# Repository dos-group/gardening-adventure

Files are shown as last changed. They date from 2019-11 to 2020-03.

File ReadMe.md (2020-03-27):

Documentation for Urban Gardening

# Table of Contents

- [Table of Contents](#table-of-contents)
- [Introduction](#introduction)
- [Prerequisites & Components](#prerequisites--components)
  - [Components listed per greenhouse](#components-listed-per-greenhouse)
- [Initial Setup](#initial-setup)
- [Installation & Setup](#installation--setup)
  - [Mesh Gateway Setup](#mesh-gateway-setup)
  - [Mesh Node Setup](#mesh-node-setup)
  - [Setting up the Cloud Environment](#setting-up-the-cloud-environment)
    - [Helm Deployment](#helm-deployment)
    - [Post Deployment Steps](#post-deployment-steps)
      - [Connecting Grafana with Influxdb](#connecting-grafana-with-influxdb)
      - [Grafana Charts](#grafana-charts)
      - [Grafana Alerts](#grafana-alerts)
        - [Create a Telegram Altert](#create-a-telegram-altert)
  - [Setting up the Greenhouse Environment](#setting-up-the-greenhouse-environment)
    - [Connecting Sensors](#connecting-sensors)
  - [Docker Sensor Images](#docker-sensor-images)
    - [Camera Configuration Options](#camera-configuration-options)
    - [Start Sensor and Actuators](#start-sensor-and-actuators)
- [Reference](#reference)

# Introduction

This project provides an infrastructure to implement a self sustaining smart garden. It uses state-of-the-art technologies to implement a variety of useful tools to monitor, alert and explore on the basis of the data.
The core of our work is the implementation of a greenhouse which provides sensors and actuators controlled via cloud systems to provide an optimal environment for plants.

In figure 1 we can see in the general overview the idea to connect multiple greenhouses via a wifi network mesh to a Cloud service. Whereby particular greenhouses can serves as a gateway and are directly connected to the cloud.
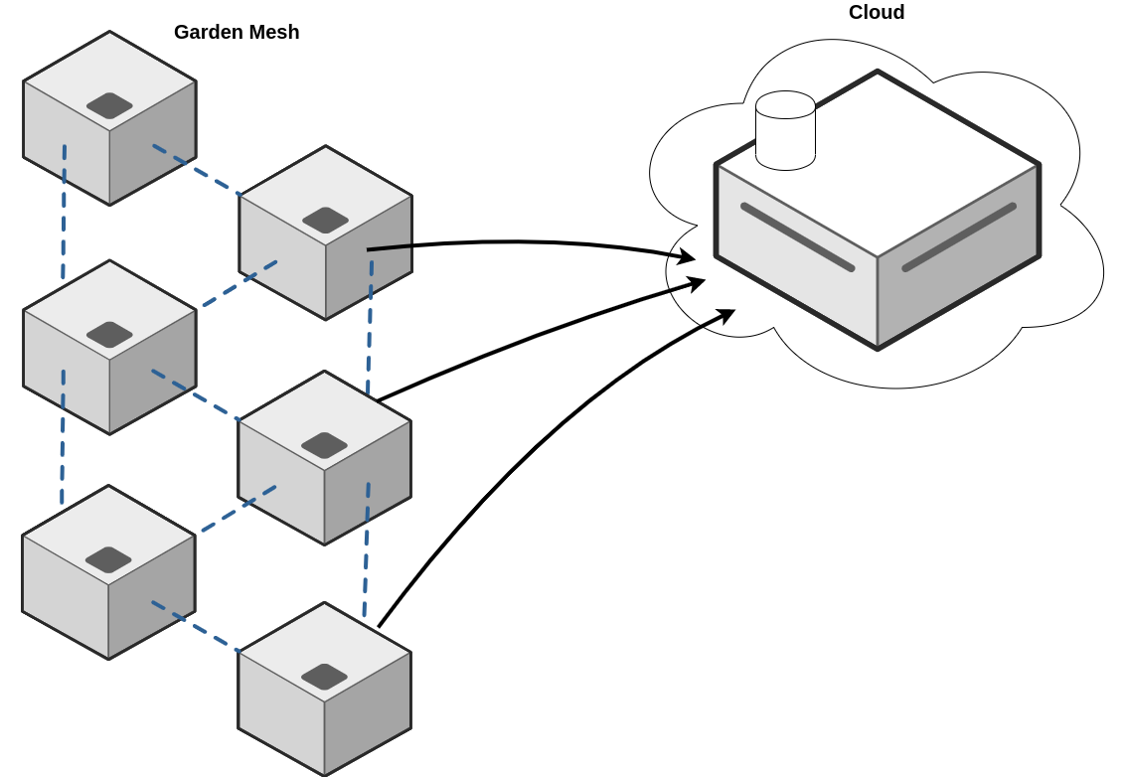
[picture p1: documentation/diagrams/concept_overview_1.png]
Overview


The greenhouses themselves contain a variety of sensors and actuators, as shown in figure 2. These sensors and actuators are connected via the GPIO connectors to an Raspberry pi.  The Raspberry pi gathers the sensor data and distributes this data via the above mentioned mesh network. The Pi also receives instructions for the connected actuators and executes them.
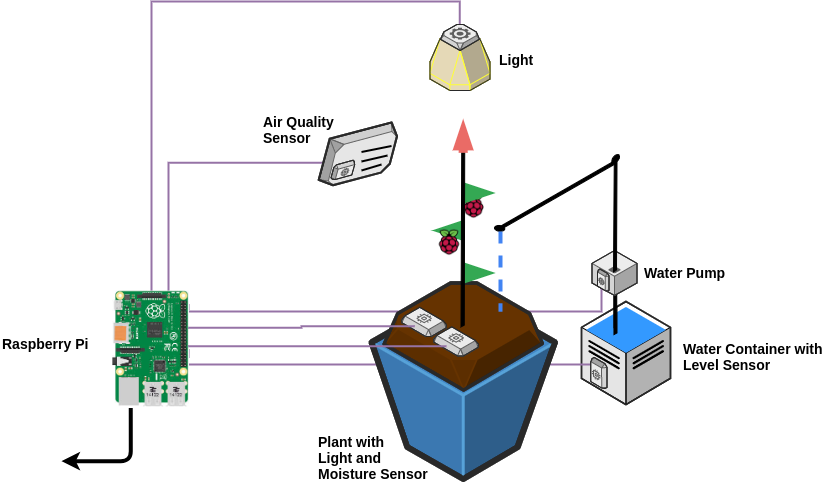
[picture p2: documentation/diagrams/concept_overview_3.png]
Overview


Figure 3 gives an overview about the Software implementation. In the lower part we see Multiple Pi's which implement the mesh network via [B.A.T.M.A.N](https://www.open-mesh.org/projects/open-mesh/wiki) (better approach to mobile ad-hoc networking) is a routing protocol for multi-hop ad-hoc mesh networks. The sensor & actuator logic is implemented via Python and containerized in [Docker](https://www.docker.com/). Each Raspberry is a Worker Node in a [K3s](https://k3s.io/) cluster.  K3s is a lightweight Kubernetes built for IoT & Edge computing. It perfect to for running on something as small as a Raspberry Pi.  
The sensor communication is realized via [MQTT](http://mqtt.org/). In particular we use [Paho mqtt](https://www.eclipse.org/paho/) for pyhton on the Pi side and a Mosquitto MQTT Broker on the cloud side. 
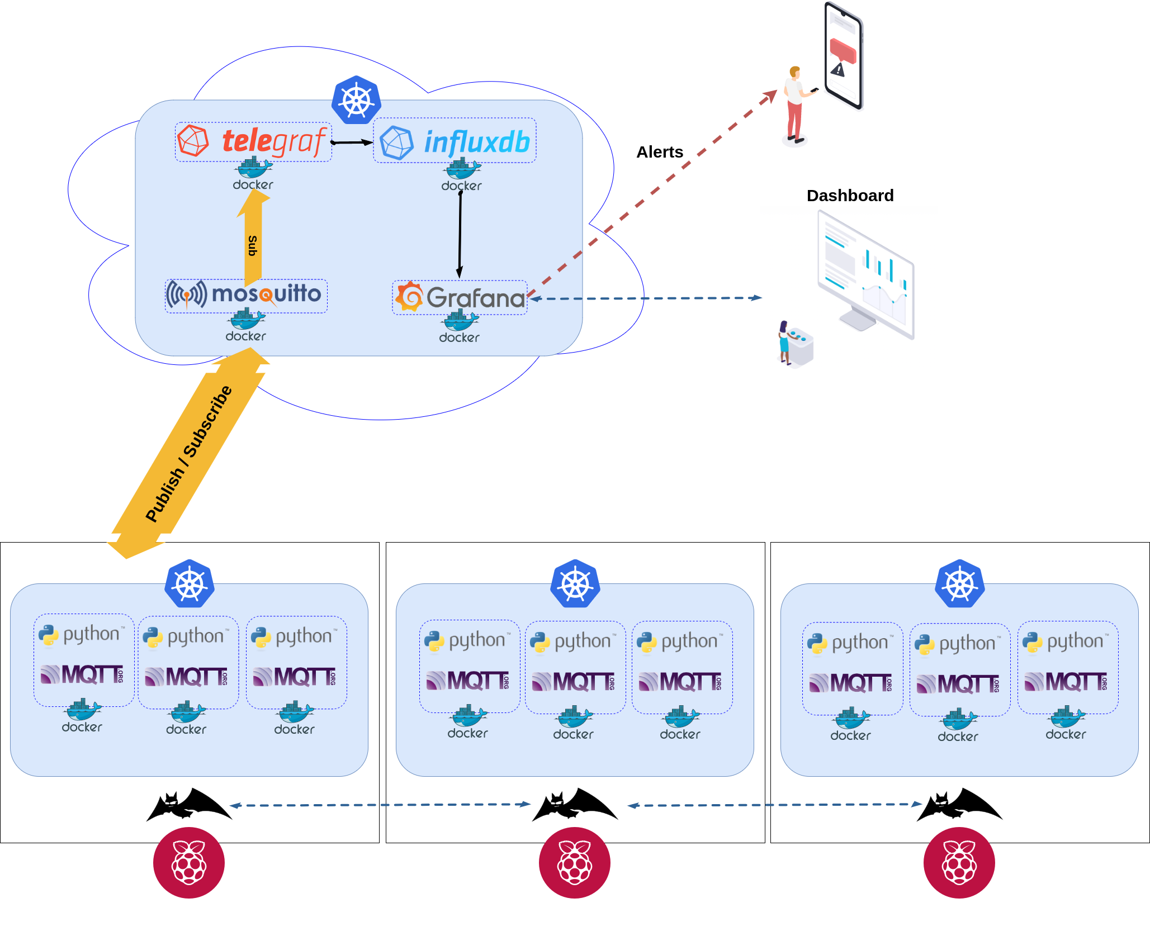
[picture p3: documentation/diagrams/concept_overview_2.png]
Overview

The cloud environment  consists of four services. A [Mosquitto](https://mosquitto.org/man/mqtt-7.html) MQTT broker for the communication with the greenhouse instances. [Telegraf](https://www.influxdata.com/time-series-platform/telegraf/) which subscribes to the published topics by the greenhouse sensors and  saves the data in an [influxdb](https://www.influxdata.com/) database. And lastly [Grafana](https://grafana.com/) which is used for data visualization and alerting.

# Prerequisites & Components

For the creation of the project we used a desktop computer as cloud environment(Master node) and raspberry pi's as worker nodes

## Components listed per greenhouse

| Component | Description |
| --- | --- |
| Raspberry Pi 3B / 4 | - |
| MicroSD Card 32GB | - |
| DHT22 Sensor | Temperature & Humidity Sensor |
| Water Level Sensor | Analog Water Level Sensor |
| Soil Moisture Sensor | Analog Soil Moisture Sensor |
| LDR | Light Dependent Resistor |
| MCP3008 | 8 Channel 10-bit ADC |
| Breadboard | 1 Piece |
| Male to Male Connectors | 100 Pieces |
| Male to Female Connectors | 100 Pieces |
| 5v Power Supply | Power supply for Raspberry Pi. 2.5A Power Supply recommended |
| 5v Waterpump | Water pump (Not implemented) |
| RGB LED | NeoPixel Ring - 12 x RGB LED |
| Jumper-Cabel | 5v power supply for LED |

# Initial Setup

Custom raspbian OS creation is part of this repository which installs necessary packages and configurations for setting up `gateway` and `node` Pis respectively. The configuration files are listed under the folder `batman`. These files could further be modified according to the needs of the project. Also the image creation, requires Ubuntu/Debian OS.

To create an image:

1. Clone this git repository

2. Run the script build-batman-node.sh in the folder `garden-adventure`

  ```bash
        ./build-batman-node.sh -t [gateway|node] -n [hostname] -u [k3s_url] -k [k3s_token] -d [dns_ip]
  ```

Specify the required options for the above command(type, hostname, k3s url, k3s token). Mention your dns_ip when creating an image for `node`(eg: 8.8.8.8).

* The above command downloads the base image of raspbian STRETCH. This base image can be modified as per the needs by changing the base image url in the file `build-raspbian`.
* Further, the command creates two installation scripts under the root user as part of each image(gateway/node).
* Root user is created with the password `raspberry`. This can also be modified in the file `build-batman-node.sh`
* The image created, has only limited firmwares installed that are necessary for the project(`brcm` for wlan interface). Other firmwares could be installed from [here](https://github.com/RPi-Distro/firmware-nonfree). They should be copied at the time of image creation. Refer the script `build-batman-node.sh`.

# Installation & Setup

Using Raspberry Pi Imager, burn the created image onto a SD card. The created image could be found under the folder `images` after running above script.

- Writing the Raspbian Image to the SD Card
  - [Windows](https://www.raspberrypi.org/documentation/installation/installing-images/windows.md)
  - [Linux](https://www.raspberrypi.org/documentation/installation/installing-images/linux.md)
  - [MacOS](https://www.raspberrypi.org/documentation/installation/installing-images/mac.md)
  - [ChromeOS](https://www.raspberrypi.org/documentation/installation/installing-images/chromeos.md)

## Mesh Gateway Setup

First setup the gateway Pi by connecting it to ethernet and inserting the SD card that contains the raspbian OS for gateway and powering it on. The first boot steps will be performed and you can login with the details provided above. Under the root user following scripts can be found:

1. smart-garden-mesh.sh

2. k3s_installation.sh

Running the first script, brings up the B.A.T.M.A.N inteface for mesh network along with the Pi configured as a gateway. It starts a dhcp server for the inteface `bat0` and enables a custom service called `port-forwarding.service` that forwards packets across batman and ethernet interface.

Running the second script, installs K3s and adds the Pi as a worker to a K3s cluster. If the k3s master is not part of the same network as gateway and belongs to the public network, then k3s installation should be done via VPN. This is currently out of the scope of this repository. Refer [OpenVPN](https://openvpn.net/) or [Wiregaurd](https://www.wireguard.com/) for more information about setting up VPN.

## Mesh Node Setup

Setup the node by inserting the SD card that contains the raspbian OS for the node. The ethernet connection is not needed for the node setup. Also under the root user, the above mentioned scripts could be found.

1. First run smart-garden-mesh.sh to setup the B.A.T.M.A.N

2. Wait until the interface `bat0` gets an ip address from DHCP server within the range `172.27.0.100 - 172.27.0.200`. This may take a time of 20-30s.

3. Before running the K3s installation script, make sure the k3s master can direct packets to the node using `ping` command. If the packet loss is 100%, then you need to add necessary route in the k3s master using the command `ip`.

Eg: ``` ip route add 172.27.0.0/24 via 192.168.10.74 dev eth0 ```

## Setting up the Cloud Environment

This chapter describes the implementation of the Cloud services. In detail the installation of Grafana, Influxdb, Mosquitto MQTT Broker and Telegraf.

We use for all the cloud service installations [Helm](https://helm.sh) scripts. For the installation of Helm, please refer to the [documentation](https://helm.sh/docs/intro/quickstart/).

**Notice:** We used for all services the standard username: "admin" and password: "dspj2020"

### Helm Deployment

First add the Mosquitto Broker helom chart via: ` helm repo add smizy https://smizy.github.io/charts`
To start the services you can run the script in `gardening-adventure/cloud_garden/deployment/cloud_deployment.sh` This will start [Grafana](https://github.com/helm/charts/tree/master/stable/grafana), [Influxdb](https://github.com/helm/charts/tree/master/stable/influxdb), [Mosquitto MQTT Broker](https://github.com/smizy/charts/tree/master/mosquitto) and [Telegraf](https://github.com/helm/charts/tree/master/stable/telegraf) via helm. 

**Notice**: This will start the services without any node selection. For that edit the corresponding settings in the yaml files.  For adding a label to a node use the following command : `kubectl label nodes <nodename> <key>=<value> --overwrite`

### Post Deployment Steps
The Section gives examples for possible post deployment application of the services. This includes Database connections, charts and alerts.
#### Connecting Grafana with Influxdb

Login to the grafana UI. Use `kubectl get svc` to get the IP's and ports of all services.

1. Login to the Grafana Dashboard
2. Click the gear wheel icon on the left site and  select "Data Sources"
3. click "Add data source"
4. Choose Influxdb
5. Add the influxDB url `hhtp://<Influxdb IP>:8086`
6. Use `garden` as database
7. The default influxdb user is `admin` and password is `dspj2020`
8. Click `Save and Test`

#### Grafana Charts

After the datasource has been added the next step is to add the dashboard which displays the data from the datasource.

1. To create a Grafana dashboard click on `New dashboard`(Create -> New Dashboard -> Graph).
2. Click on Panel Title -> Edit. A new window with the graph will open up. Here we select the metric we would want to display in the graph. I will use the Temperature as an example.
3. Pick the data source that was defined earlier in the data source field. Tip: This should be influxdb datasource.
4. edit the query as follows -> in the `FROM` line, select the sensor name in the second dropdown. This will be the sensor that the graph will depict values from. In the `SELECT` line, pick the appropriate field, for example `temperature`. Pick the desired grouping time interval on line 3 and save the graph by clicking the save icon on the top right hand side.
5. Check the visibility of the data on the dashboard, the data should be available as a graph.
6. Repeat these steps for every data available from the sensors.

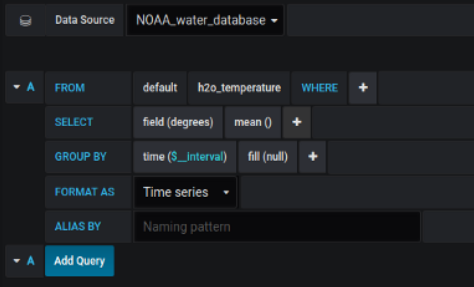
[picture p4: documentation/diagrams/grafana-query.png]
Dashboard Query


#### Grafana Alerts

We used [Grafana's Alerts](https://grafana.com/docs/grafana/latest/alerting/rules/) to receive [notifications](https://grafana.com/docs/grafana/latest/alerting/notifications/) when, for example, humidity drops below a certain level.
As an example we show here to configure an alert sent to telegram. For more options please have a look at the Grafana's alert documentation.

##### Create a Telegram Altert

1. Created a bot via @BotFather, and get an API token in telegram
2. Create new Chat Group in Telegram App, for example: “Super Dooper Alert Group” with people who need to be alerted.
3. Invite your bot to this group
4. Type at least one message in that group,  **this is very important**
5. Use cURL or just place this on any Browsers Address Bar: `https://api.telegram.org/bot<TOKEN>/getUpdates`
This should return an JSON object, you need to find key “chat” like this one:  
`"chat":{"id":-456343576,"title":"Super Dooper Alert Group","type":"group","all_members_are_administrators":true}`
6. Login to grafana
7. Click to the left Bell icon
8. Add notification channel
9. Select Telegram
10. Enable/disable settings you preger
11. Put Telegram API token to he fiel
12. Add chat ID (it starts with -, and that needs too)
13. Click Test notification
14. Save it.
15. Create a rule in the moister graph panel panel
16. Go to dashboard
17. Select the desired Graph
18. Click Alarm icon
19. Click "Create Alert"

## Setting up the Greenhouse Environment

This chapter describes the installation of a new smart greenhouse.
The installation includes the hardware and the software configuration of the sensors/actuators and the Pi. 

### Connecting Sensors

Figure 4 shows the wiring of the sensors with the Raspberry Pi. Please note that an external 5V power supply is required when using several sensors and actuators. This is especially true if you use an LED light or a water pump.
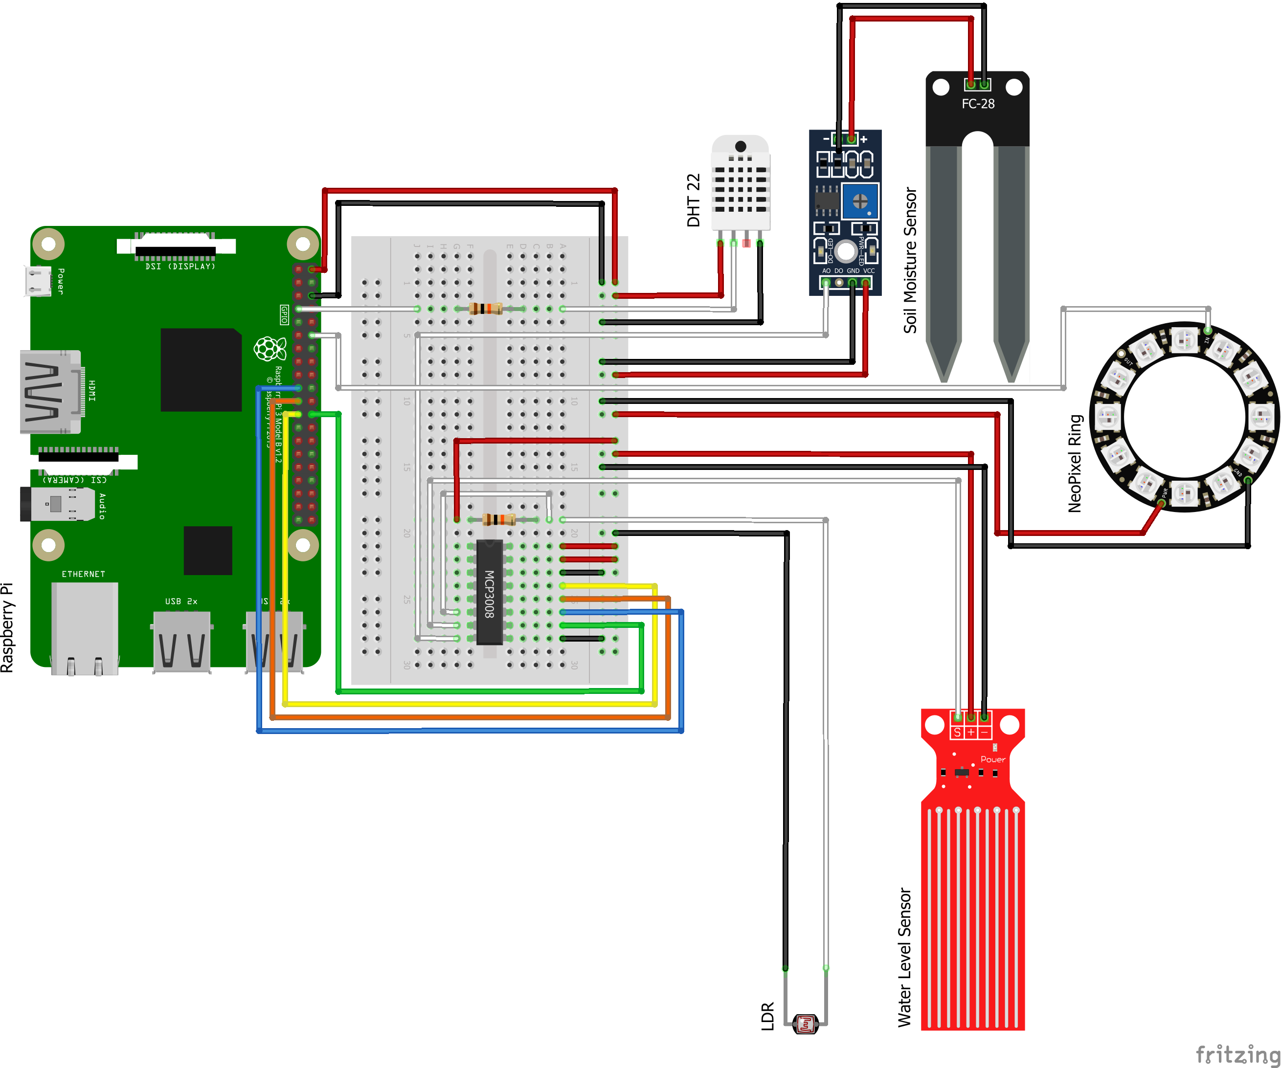
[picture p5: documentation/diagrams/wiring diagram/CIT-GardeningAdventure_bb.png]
Wiring Diagram


## Docker Sensor Images

Each sensor has its own docker image. We use [Balenalib Raspbian](https://hub.docker.com/r/balenalib/rpi-raspbian) images which is optimized for the use in IoT devices. Use the -f option in the scripts directory to make sure Docker finds all the files it needs.
Example to build the dht sensor:

       .../gardening-adventure/scripts$ docker build -f dht_sensor/Dockerfile -t dht .

### Camera Configuration Options

The Raspberry Pi Camera module supports a variety of resolutions, ISO settings, Interval between Capture of Photos. All of these parameters are configurable. The camera_module.yml file takes all these parameters and deploys the camera module with the parameters requested. In the `spec` section, under `container` section, the options for the camera can be set under `arguments` section.

If no options under this section is set in the camera_module.yml file, the camera module is deployed with the default values. The default values and the supported values are described in the table below.

| Argument | Description | Supported Values | Default Value |
| --- | --- | --- | --- |
| resolution | Image resolution | 1920-1080, 3280-2464, 1640-1232, 1640-922, 1280-720, 640-480 | 1920-1080 |
| output | Location to store output. | Any valid *nix path | /camera_output/continuous_captures/ |
| interval | Number of seconds between captures. | Must be an Integer. | 10 |
| iso | ISO Sensitivity Settings | 100 - 800 | 100 |

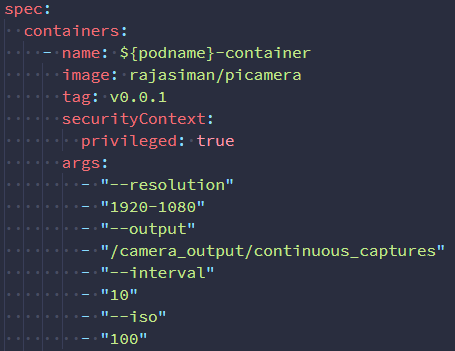
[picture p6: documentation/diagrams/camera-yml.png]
Camera Configuration


### Start Sensor and Actuators

If all required sensors are wired you can continue with the software installation. The installation of the desired devices is happening via a shell script. For that it is required that K3s is running on the Pi controlling the sensors and the IP address for the MQTT Broker is known.
To start the Sensors run the  ```gardening-adventure/scripts/sensor_deployment.sh``` script in an environment with [kubectl](https://kubernetes.io/docs/tasks/tools/install-kubectl/#verifying-kubectl-configuration) configured. After the deployment the sensors immediately start sending data to the MQTT Broker
**Note:** if you use your own Docker image reposetory please change this in the yml files.
# Reference

1. B.A.T.M.A.N installation and setup - [link](https://medium.com/@tdoll/how-to-setup-a-raspberry-pi-ad-hoc-network-using-batman-adv-on-raspbian-stretch-lite-dce6eb896687)
2. Raspbian image creation - [link](https://github.com/jonesinator/raspbian-remaster)
3. Dhcp configuration - [link](https://www.howtoforge.com/tutorial/install-and-configure-isc-dhcp-server-in-debian-9/)

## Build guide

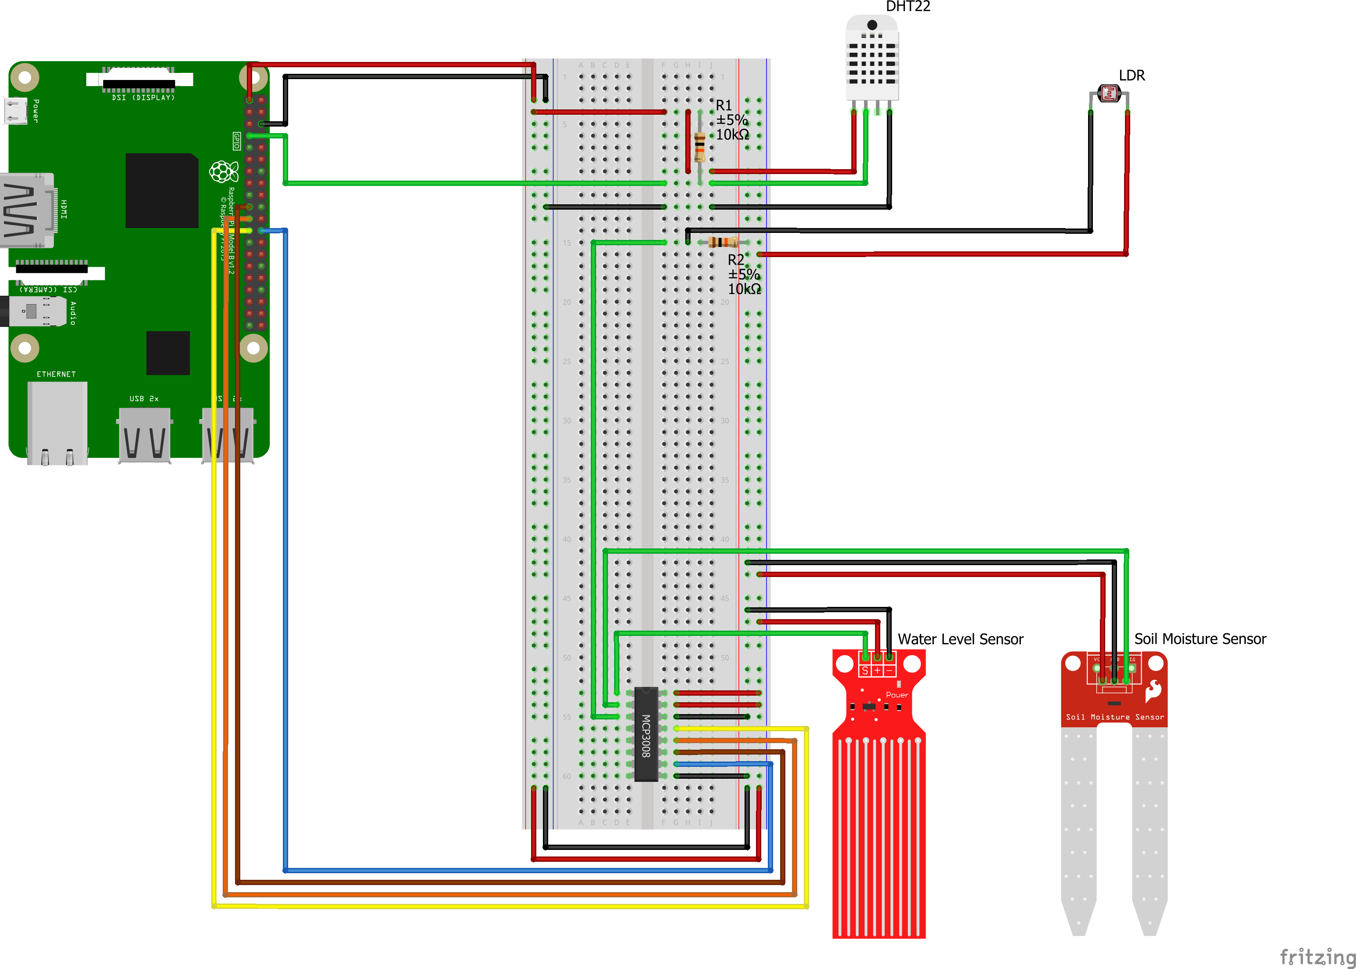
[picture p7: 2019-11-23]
documentation/diagrams/wiring diagram/Wiring Diagram_bb.png

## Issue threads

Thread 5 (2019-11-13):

Install K3s

P2W2, 2019-11-13:
Install k3s on Pi's and get familiar with deployment workflow, kubectl and so on

We plan to use k3s for the Kubernetes cluster deployed on all Pi's and the central server, you can use the following links
to read up on k3s:

https://k3s.io/ -> Project Website with documentation on how to deploy k3s
https://github.com/rancher/k3os -> Linux distribution designed to run k3s
https://github.com/alexellis/k3sup -> can be used to deploy k3s on VM's and other devices
Some Blogposts describing the deployment of k3s on Raspberry Pi's:
https://medium.com/@mabrams_46032/kubernetes-on-raspberry-pi-c246c72f362f https://www.danielstechblog.io/running-a-kubernetes-cluster-with-k3s-on-raspbian/
* http://collabnix.com/get-started-with-k3s-a-lightweight-kubernetes-distribution-for-raspberry-pi-cluster/

Some Blogposts about deploying a Mesh network with Raspberry Pi's:
https://medium.com/swlh/setting-up-an-ad-hoc-mesh-network-with-raspberry-pi-3b-using-batman-adv-1c08ee565165 https://medium.com/@tdoll/how-to-setup-a-raspberry-pi-ad-hoc-network-using-batman-adv-on-raspbian-stretch-lite-dce6eb896687
https://tomesh.net/build-a-node/ https://hackaday.com/2012/11/14/mesh-networking-with-multiple-raspberry-pi-boards/

In case of questions or problems feel free to drop us a mail.

alexellis, 2019-12-10:
Let me know if I can be of help. #k3sup is a nice tool for installing k3sup, but also helm charts after that.

Closed 2019-11-15.

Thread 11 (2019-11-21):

Pre configurated Raspberry pi Image.

rajasiman, 2019-11-21:
Batman, SSH etc.

rajasiman, 2019-11-22:
https://medium.com/swlh/headless-raspberry-pi-part-1-installing-configuring-raspbian-b8714a767259

rajasiman, 2019-11-22:
https://medium.com/platformer-blog/creating-a-custom-raspbian-os-image-for-production-3fcb43ff3630

More like configure everything on one and clone the image to other devices.

rajasiman, 2019-11-22:
https://www.raspberrypi.org/blog/pibakery/

rajasiman, 2019-11-22:
https://github.com/RPi-Distro/pi-gen
https://learnthinksolvecreate.wordpress.com/category/raspberry-pi/pi-gen/
http://kmdouglass.github.io/posts/create-a-custom-raspbian-image-with-pi-gen-part-1/

rajasiman, 2019-11-22:
https://github.com/TheSin-/rpi-img-builder

This looks **very** promising.

Plugins:
It should be fairly easy to customize your image for your own needs. Building and adding plugins is easy. Each plugin can contain:

- packages: file with one line containing debian packages to install
- preinst: script to run pre chroot
- postinst: script to run in chroot of the rootfs
- files: dir which contains files to be copied into the rootfs, perms and atts included
- patches: dir which contains patch files to apply to the rootfs
- baseonly: is a special file for repo plugins, if the file exists the plugin is only included if the repo is the base repo

rajasiman, 2019-11-22:
https://raspberrypi.stackexchange.com/questions/855/is-it-possible-to-update-upgrade-and-install-software-before-flashing-an-image

shri-hari93, 2020-02-24:
Custom Pi image
- [ ] Latest pi OS image
- [ ] Enable SSH
- [ ] Batman installation
- [ ] Gateway configuration / Node configuration
- [ ] Initiate batman interface using script
- [ ] Assign Ip address (dhcp/avahi-autoipd)
- [ ] Install K3S agent using token

srnbckr, 2020-03-11:
Are there any updates on this?

shri-hari93, 2020-03-11:
@srnbckr I have created a couple of images will have to test with k3s cluster tomorrow at your office.

Closed 2020-03-27.

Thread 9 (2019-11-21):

please check for the red marked sensors in the google docs, if you can find appropiate sensors on the following sides:

P2W2, 2019-11-21:
[GooGle Doc](https://docs.google.com/document/d/1Rr977Y6NMDTuLg9P6otBDmeE8tLGlXRtDigQU-5CEXU/edit?usp=sharing )
[Google Doc with Item Links](https://docs.google.com/document/d/1kNQiLh6pq2x9lESNbOEtW0LJluIDak8VAkCuGwdTtOM/edit?usp=sharing)
----------------Sites--------------------
https://www.adafruit.com/, https://eckstein-shop.de/, https://www.ti.com/, https://www.mouser.de, reichelt and conrad are also okay.

rajasiman, 2019-11-21:
waiting on florian's reply, we still do not know the list of parts already ordered. Once that i clear, we can filter the not yet ordered stuff.

rajasiman, 2019-11-23:
After yesterday's discussion with Florian, I think we have all of it ordered. I will close this ticket.

Closed 2019-11-23.

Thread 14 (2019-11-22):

test sensor connections

rajasiman, 2019-11-22:
DHT22
Water Level sensor

rajasiman, 2019-11-22:
https://gpiozero.readthedocs.io/

rajasiman, 2019-11-22:
https://www.raspberrypi.org/documentation/usage/gpio/

rajasiman, 2019-11-22:
https://thejeswarareddyr.blogspot.com/2016/03/how-to-connect-mp3002mcp3008-adc-chip.html

rajasiman, 2019-11-22:
https://www.rototron.info/raspberry-pi-analog-water-sensor-tutorial/

rajasiman, 2019-11-22:
https://www.linuxnorth.org/raspi-sump/

rajasiman, 2019-11-22:
https://pimylifeup.com/raspberry-pi-humidity-sensor-dht22/

rajasiman, 2019-11-23:
DHT22 logging works. https://gist.github.com/rajasiman/cef147470c689e3fd4a97e73edcb7949
Water Level Sensor pending.

rajasiman, 2019-11-23:
Water Level Sensor:
Wiring:
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
https://github.com/adafruit/Adafruit_CircuitPython_MCP3xxx/

rajasiman, 2019-11-23:
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
All sensors with wiring

Closed 2019-11-23.

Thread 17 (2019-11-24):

Technology decisions/additions

rajasiman, 2019-11-24:
Should we look at using the TICK stack? At the very least the T along with the I from TICK.

Telegraf (Developed by Influxdata)
> https://www.influxdata.com/time-series-platform/telegraf/
**IoT sensors**
Collect critical stateful data (pressure levels, temp levels, etc.) from IoT sensors and devices.
**Systems**
Collect metrics from your modern stack of cloud platforms, containers, and orchestrators.

Message Queue:
> https://www.rabbitmq.com/
**Asynchronous Messaging**
Supports multiple messaging protocols, message queuing, delivery acknowledgement, flexible routing to queues, multiple exchange type.

All of the stuff listed above makes it A LOT easier for us.

rajasiman, 2019-11-24:
Also what about this... Oops.

https://docs.influxdata.com/platform/integrations/kubernetes/#should-i-run-influxdb-in-kubernetes

P2W2, 2020-01-16:
MIGT Stack --> mqtt, influxDB, Grafana, telegraf
:)

Closed 2020-01-16.

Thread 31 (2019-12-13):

short presentation

P2W2, 2019-12-13:
architecture
what we have done so far
benchmarks
show dashboards with sensor data

P2W2, 2019-12-14:
Duplicate [#25](url)

Closed 2019-12-14.

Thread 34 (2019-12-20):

Configure Kubernetes Environment

P2W2, 2019-12-20:
Deploy:
Grafana, telegraf, influxDB and Mosquitto-mqtt on the master node.

Deploy sensor Docker images on the raspberry's pi

P2W2, 2020-01-23:
## Assosiate Node with pod
`kubectl label nodes peewee-thinkpad dasboard=grafana --overwrite
`
## Grafana
`helm install grafana-garden -f grafana.yaml --set nodeSelector.dasboard=grafana stable/grafana
`
## InfluxDB
`helm install influxdd-garden -f influxdb.yaml --set nodeSelector.databases=influxdb stable/influxdb
`
## Mosquitto
`helm install mosquitto-garden -f mosquitto.yaml --set nodeSelector.mqttt=mosquitto smizy/mosquitto
`
`kubectl expose pod ll mosquitto-garden... --port=1883 --target-port=188
`
## Telegraf
`helm install telegraf-garden -f telegraf.yaml stable/telegraf`

rajasiman, 2020-01-23:
https://github.com/smizy/charts/issues/4

FYI

Closed 2020-01-30.

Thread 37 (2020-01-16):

Create the Docker Images for the Sensors

P2W2, 2020-01-16:
- [x] Water Sensor
- [x] Soil Sensor
- [x] Air Sensor
- [x] Light Sensor
- [x] Camera Sensor
- [x] Light

P2W2, 2020-01-16:
- [ ] Water Sensor
- [ ] Air Sensor
- [ ] Soil Sensor
- [ ] Light Sensor
- [ ] Camera Sensor

Closed 2020-03-05.

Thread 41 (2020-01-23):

deploy fully equipped raspberry

P2W2, 2020-01-23:
- [x] Water Sensor
- [x] Soil Sensor
- [x] Air Sensor
- [x] Light Sensor
- [x] Camera Sensor
- [x] Light

P2W2, 2020-02-06:
- [ ] Waterlevel

- [ ] Air sensor

- [ ] Light sensor

- [ ] Moisture sensor

- [ ] Light

- [ ] Waterpump

Closed 2020-03-05.

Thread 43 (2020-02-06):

Implement light logic

P2W2, 2020-02-06:
Implement  the Logic for:

- [x] light sensor and Light

Both implementations should turn on/off the actuators on basis of sensor values

P2W2, 2020-03-05:
The waterpumps are still missing.
Buy Waterpumps

Closed 2020-03-05.

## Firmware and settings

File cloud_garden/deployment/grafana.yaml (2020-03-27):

rbac:
  create: true
  pspEnabled: true
  pspUseAppArmor: true
  namespaced: false
  extraRoleRules: []
  # - apiGroups: []
  #   resources: []
  #   verbs: []
  extraClusterRoleRules: []
  # - apiGroups: []
  #   resources: []
  #   verbs: []
serviceAccount:
  create: true
  name:
  nameTest:
#  annotations:

replicas: 1

## See `kubectl explain poddisruptionbudget.spec` for more
## ref: https://kubernetes.io/docs/tasks/run-application/configure-pdb/
podDisruptionBudget: {}
#  minAvailable: 1
#  maxUnavailable: 1

## See `kubectl explain deployment.spec.strategy` for more
## ref: https://kubernetes.io/docs/concepts/workloads/controllers/deployment/#strategy
deploymentStrategy:
  type: RollingUpdate

readinessProbe:
  httpGet:
    path: /api/health
    port: 3000

livenessProbe:
  httpGet:
    path: /api/health
    port: 3000
  initialDelaySeconds: 60
  timeoutSeconds: 30
  failureThreshold: 10

## Use an alternate scheduler, e.g. "stork".
## ref: https://kubernetes.io/docs/tasks/administer-cluster/configure-multiple-schedulers/
##
# schedulerName: "default-scheduler"

image:
  repository: grafana/grafana
  tag: 6.5.2
  pullPolicy: IfNotPresent

  ## Optionally specify an array of imagePullSecrets.
  ## Secrets must be manually created in the namespace.
  ## ref: https://kubernetes.io/docs/tasks/configure-pod-container/pull-image-private-registry/
  ##
  # pullSecrets:
  #   - myRegistrKeySecretName

testFramework:
  enabled: true
  image: "dduportal/bats"
  tag: "0.4.0"
  securityContext: {}

securityContext:
  runAsUser: 472
  fsGroup: 472


extraConfigmapMounts: []
  # - name: certs-configmap
  #   mountPath: /etc/grafana/ssl/
  #   subPath: certificates.crt # (optional)
  #   configMap: certs-configmap
  #   readOnly: true


extraEmptyDirMounts: []
  # - name: provisioning-notifiers
  #   mountPath: /etc/grafana/provisioning/notifiers


## Assign a PriorityClassName to pods if set
# priorityClassName:

downloadDashboardsImage:
  repository: appropriate/curl
  tag: latest
  pullPolicy: IfNotPresent

downloadDashboards:
  env: {}

## Pod Annotations
# podAnnotations: {}

## Pod Labels
# podLabels: {}

podPortName: grafana

## Deployment annotations
# annotations: {}

## Expose the grafana service to be accessed from outside the cluster (LoadBalancer service).
## or access it from within the cluster (ClusterIP service). Set the service type and the port to serve it.
## ref: http://kubernetes.io/docs/user-guide/services/
##
service:
  type: NodePort
  port: 3000
  nodePort: 30000
  targetPort: 3000
    # targetPort: 4181 To be used with a proxy extraContainer
  annotations: {}
  labels: {}
  portName: service

ingress:
  enabled: false
  annotations: {}
    # kubernetes.io/ingress.class: nginx
    # kubernetes.io/tls-acme: "true"
  labels: {}
  path: /
  hosts:
    - chart-example.local
  ## Extra paths to prepend to every host configuration. This is useful when working with annotation based services.
  extraPaths: []
  # - path: /*
  #   backend:
  #     serviceName: ssl-redirect
  #     servicePort: use-annotation
  tls: []
  #  - secretName: chart-example-tls
  #    hosts:
  #      - chart-example.local

resources: {}
#  limits:
#    cpu: 100m
#    memory: 128Mi
#  requests:
#    cpu: 100m
#    memory: 128Mi

## Node labels for pod assignment
## ref: https://kubernetes.io/docs/user-guide/node-selection/
#
nodeSelector: {}

## Tolerations for pod assignment
## ref: https://kubernetes.io/docs/concepts/configuration/taint-and-toleration/
##
tolerations: []

## Affinity for pod assignment
## ref: https://kubernetes.io/docs/concepts/configuration/assign-pod-node/#affinity-and-anti-affinity
##
affinity: {}

extraInitContainers: []

## Enable an Specify container in extraContainers. This is meant to allow adding an authentication proxy to a grafana pod
extraContainers: |
# - name: proxy
#   image: quay.io/gambol99/keycloak-proxy:latest
#   args:
#   - -provider=github
#   - -client-id=
#   - -client-secret=
#   - -github-org=<ORG_NAME>
#   - -email-domain=*
#   - -cookie-secret=
#   - -http-address=http://0.0.0.0:4181
#   - -upstream-url=http://127.0.0.1:3000
#   ports:
#     - name: proxy-web
#       containerPort: 4181

## Enable persistence using Persistent Volume Claims
## ref: http://kubernetes.io/docs/user-guide/persistent-volumes/
##
persistence:
  type: pvc
  enabled: true
  # storageClassName: default
  accessModes:
    - ReadWriteOnce
  size: 2Gi
  # annotations: {}
  finalizers:
    - kubernetes.io/pvc-protection
  # subPath: ""
  # existingClaim:
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

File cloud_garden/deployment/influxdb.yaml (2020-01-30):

## influxdb image version
## ref: https://hub.docker.com/r/library/influxdb/tags/
image:
  repository: "influxdb"
  tag: "1.7.6-alpine"
  pullPolicy: IfNotPresent
  ## If specified, use these secrets to access the images
  # pullSecrets:
  #   - registry-secret

## Customize livenessProbe and readinessProbe
## ref: https://docs.influxdata.com/influxdb/v1.7/tools/api/#ping-http-endpoint
##
livenessProbe:
  probePath: "/ping"

readinessProbe:
  probePath: "/ping"

startupProbe:
  enabled: false
  probePath: "/ping"
  # failureThreshold: 6
  # periodSeconds: 5

## Specify a service type
## NodePort is default
## ref: http://kubernetes.io/docs/user-guide/services/
##
service:
  ## Add annotations to service
  # annotations: {}
  type: ClusterIP
  ## Add IP Cluster
  # clusterIP: ""
  ## Add external IPs that route to one or more cluster nodes
  # externalIPs: []
  ## Specify LoadBalancer IP (only allow on some cloud provider)
  # loadBalancerIP: ""
  ## Allow source IPs to access on service (if empty, any access allow)
  # loadBalancerSourceRanges: []

## Persist data to a persistent volume
##
persistence:
  enabled: true
  ## influxdb data Persistent Volume Storage Class
  ## If defined, storageClassName: <storageClass>
  ## If set to "-", storageClassName: "", which disables dynamic provisioning
  ## If undefined (the default) or set to null, no storageClassName spec is
  ##   set, choosing the default provisioner.  (gp2 on AWS, standard on
  ##   GKE, AWS & OpenStack)
  ##
  # storageClass: "-"
  annotations:
  accessMode: ReadWriteOnce
  size: 2Gi

## Deploy InfluxDB Enterprise - License required
## ref: https://www.influxdata.com/products/influxdb-enterprise/
enterprise:
  enabled: false
  licensekey: {}
  clusterSize: 4
  meta:
    image:
      ## This image contains the enterprise meta node package for clustering.
      ## It is meant to be used in conjunction with the influxdb:data package of the same version.
      ## ref: https://hub.docker.com/_/influxdb
      tag: meta
    clusterSize: 3
    ## seed is hashed and used as `internal-shared-secret` for Meta service.
    seed: dead-beef-cafe-bae
    ## Configure resource requests and limits
    ## ref: http://kubernetes.io/docs/user-guide/compute-resources/
    resources: {}
  #  resources:
  #    requests:
  #      memory: 512Mi
  #      cpu: 2
  #    limits:
  #      memory: 1Gi
  #      cpu: 4

## Create default user through Kubernetes job
## Defaults indicated below
##
setDefaultUser:
  enabled: false

  ## Image of the container used for job
  ## Default: appropriate/curl:latest
  ##
  image: appropriate/curl:latest

  ## Deadline for job so it does not retry forever.
  ## Default: activeDeadline: 300
  ##
  activeDeadline: 300

  ## Restart policy for job
  ## Default: OnFailure
  restartPolicy: OnFailure

  user:

    ## The user name
    ## Default: "admin"
    username: "admin"

    ## User password
    ## single quotes must be escaped (\')
    ## Default: (Randomly generated 10 characters of AlphaNum)
    password: "dspj2020"

    ## The user name and password are obtained from an existing secret. The expected
    ## keys are `influxdb-user` and `influxdb-password`.
    ## If set, the username and password values above are ignored.
    # existingSecret: influxdb-auth

    ## User privileges
    ## Default: "WITH ALL PRIVILEGES"
    privileges: "WITH ALL PRIVILEGES"

## Configure resource requests and limits
## ref: http://kubernetes.io/docs/user-guide/compute-resources/
resources: {}
#  requests:
#    memory: 256Mi
#    cpu: 0.1
#  limits:
#    memory: 16Gi
#    cpu: 8

# Annotations to be added to InfluxDB pods
podAnnotations: {}

ingress:
  enabled: false
  tls: false
  # secretName: my-tls-cert # only needed if tls above is true
  hostname: influxdb.foobar.com
  annotations:
    # kubernetes.io/ingress.class: "nginx"
    # kubernetes.io/tls-acme: "true"

## Use an alternate scheduler, e.g. "stork".
## ref: https://kubernetes.io/docs/tasks/administer-cluster/configure-multiple-schedulers/
##
# schedulerName:

## Node labels for pod assignment
## Ref: https://kubernetes.io/docs/user-guide/node-selection/
##
nodeSelector: {}

## Affinity for pod assignment
## Ref: https://kubernetes.io/docs/concepts/configuration/assign-pod-node/#affinity-and-anti-affinity
##
affinity: {}

## Tolerations for pod assignment
## Ref: https://kubernetes.io/docs/concepts/configuration/taint-and-toleration/
##
tolerations: []
# - key: "key"
#   operator: "Equal|Exists"
#   value: "value"
#   effect: "NoSchedule|PreferNoSchedule|NoExecute(1.6 only)"

## The InfluxDB image uses several environment variables to automatically
## configure certain parts of the server.
## Ref: https://hub.docker.com/_/influxdb/
env: {}
  # - name: INFLUXDB_DB
  #   value: "demo"
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

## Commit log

2019-11-23 Add wiring diagram
    [Wiring Diagram.fzz]
2019-11-23 add wiring diagram to readme
2019-12-04 clean up
    [Wiring Diagram.fzz]
2019-12-04 insert diagrams
2019-12-14 update publish sensor data
2020-01-15 add waterlevel sensor Dockerfile
2020-01-18 containers for sensor
2020-02-06 add moisture sensor script
2020-02-06 update sensor scripts
2020-02-06 add camera
2020-02-17 add camera module files with PVC and kubernetes config
2020-02-20 updating docker file for each sensor
2020-02-27 fixing issues with sensor scripts
    [moisture.py]
2020-03-05 add sensor deployment script
2020-03-05 udpate waterlevel sensor
2020-03-05 update camera deployment
2020-03-26 remove old camera module
2020-03-27 update wiring diagram
    [CIT-GardeningAdventure.fzz]
2020-03-27 update camera settings in script
2020-03-27 update camera settings
2020-03-27 add camera config diagram
2020-03-27 add camera yml image
2020-03-27 remove camera sensor from all sensor
